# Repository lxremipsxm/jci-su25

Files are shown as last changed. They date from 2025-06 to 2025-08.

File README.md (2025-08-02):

# Card Badging Mechanical Automation

## Phases
+ **Design Phase** (5/26/25 to 5/30/25)
+ **Component Setup and Testing** (Estimated: 6/4/25 to 6/6/25; Actual: 6/2/25 to 6/20/25)
+ **Construction** (Estimated: 6/20/25 to 7/1/25)
+ **Automation** (Estimated: 7/7/25 to 7/20/25)
+ **Refinement + Adding Features**

## Goals
The primary goal of this project is to create an automation that badges card for a user in a certain order. This design must be scalable, quick, and easy to use. It should be flexible as well; my intention is to make this as easy for a team to use as possible.

---

## Design Phase 

### Protoype Design (5/26)

For my first prototype, I'm creating a solution that can badge 16 cards in quick succession. It consists of a drum rotated accurately by a stepper motor. The drum has 16 holes that fit card slots into them, which are lifted by a cam (operated by a micro servo) into the range of a stationary reader. 

In order to scale this design up, an additional cam must be placed under each new reader. Since micro servos are inexpensive, this design is simultaneously cost effective. Ideally, the larger the drum, the more readers can be incorporated.

##### Onshape

This is my first time using Onshape. I spent about a day learning Onshape and how to create models accurate to scale. I then set out to create the models by sketching designs on faces and extruding them as necessary. Throughout the process, the idea behind the design remained relatively unchanged, but I made one significant revision: making the range of motion of the cams a little larger and moving the readers further away from the cards in order to prevent interference/reading multiple cards accidentally. I've also tried to use mates in my model. `Revolute_1` and `Revolute_2` in the Onshape document are fully functional and can be animated, but Onshape does not have a way for me to test a complete workflow.

##### Print (6/2)

I've sent the `.stl` files to be printed by [Robu.in's 3D printing service](https://robu.in/product/3d-printing-service/), which I will receive within a week's time (~6/9/25). The print file is saved as `Assembly2_ver3.stl` in the `3D/` directory, and the final product will look like the contents of `Prototype_Assembly.stl`. Find the Onshape document [here](https://cad.onshape.com/documents/6fe5cb060711fa738a919116/w/fa28f828e5c3d9cb04d2cd20/e/b66991c36ce5bdb22e432e13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) (you will need to sign in to view it). 

**Updates**

6/4/25: The print has been delayed, but I will move on to testing components and creating libraries to make the final product easier to construct.

6/9/25: The print was cancelled and refunded because I provided parts that were too large for the printer. The latest print file is stored in `Assembly2_ver4.stl`, in which I've reduced the height of the card slots and increased the size of the cam lift range instead. The prints will hopefully come in by next week (6/16 to 6/20).

---

## Component Testing 

Component List (tentative): Arduino UNO(1), Tower Pro 9g Micro Servos(4), NEMA 17 Stepper motor(1), DRV8825 stepper motor driver(1), 2N7000 N-MOSFETs(4), LM2965S buck converter(1)

### Makefile (6/2)

Since I'm using a more baremetal approach with this project, I'm skipping the Arduino IDE and managing functionality by editing register contents in the ATmega328p IC on-board. Additionally, I'll be using the `avr-gcc` toolchain to compile and flash my code onto the ATmega. For this, I've written a makefile that is heavily inspired by the makefiles I've had to use in college for my embedded systems course. Find the references [here](https://github.com/ProfMcL/ECE231).

### Servos 

I couldn't find any C libraries for the micro servos, unfortunately. However, I managed to create my own simple servo library that functions exactly the same. I've used a general purpose timer on the ATmega, 16-bit Timer 2, to generate a constant Fast PWM signal with a period of 20ms, which is required by the servo according to documentation, and a duty cycle that varies between 5% and 10%. The duty cycle of this PWM wave determines the angle the servo turns to. My function is constructed in such a way that it takes an input from 0 to 180 degrees, maps it to milliseconds, and adjusts the duty cycle by changing the value the timer waits till before it sets the PWM to `LOW` again.

The next step is to create a way to control four servos with the same timer. This is possible, but it requires some tweaking of my library to include taking a servo number as input, as well as NMOSFETs in the circuit to redirect the PWM signal to these servos as required. I will also need to tweak *when* the signal is `HIGH` depending on the servo that is being addressed.

### Stepper Motor (6/9)

I'm currently waiting for the stepper motor driver to arrive (DRV8825). Until then, however, I will work on customizing a library for this driver. Find the library github repository [here](https://github.com/adrielluiz/drv8825_c/tree/main). According to the documentation, I need to provide implementations of setting pins to output and creating a `delay_us()` function. Fortunately, I can just use the `utils/delay.h` library to complete that part. 

I've included `drv8825.c` and its associated header in `lib/`, and I will modify it there. The original author has left in some misspellings of DRV8825 in method and type identifiers, which I have fixed.

The library readme recommends using a certain code structure, which I'll copy into `main.c`. 

Now, I'll modify `drv8825.c`, which contains the methods I need to customize to my chip architecture. Fortunately for me, I will need to connect 8 pins from DRV8825 into GPIO pins (the rest are for power/go into the motor directly), so I can use one full port on the ATmega, which is exactly 8 bits wide/8 pins wide. I'm going to use `PORTD`, as `PORTB` currently is being used for USART. This way, each pin on the DRV8825's right-hand side can be connected directly to PD0-PD7, making the definition of `stepper_pin_set()` incredibly easy to implement via simple bitwise operations. Since PD0-PD7 are organized perfectly in order on the board, the connections will also be satisfyingly clean.

Note that in `drv8825.h`, the `enum drv8825_drv_pins_e` typedef is ordered significantly differently than that of the original author in order to implement `stepper_pin_set()` as described.

Once the DRV8825 comes in, I can test the stepper and the driver simultaneously, and I can conclude this phase. 

Update(6/16/25): The driver component has come in. I completed testing on 6/18, primarily because I was trying to understand why my motor was not receiving any current from the drv8825 at all. Apparently I had misunderstood the pinout on the board. The pins 2A, 1A, 1B, and 2B are outputs to the stepper motor, in that order. The NEMA 17 stepper motor has four input wires, or two pairs of wires that connect to two electromagnetic coils in the inner workings of the motor. I was connecting each pair to the driver by number rather than letter; i.e. I connected one pair to 1A and 1B and another to 2A and 2B. This did not work, and I was about to return the driver, but after trying some permutations of the four wires, I realized that the combination that I needed to use was by letter, i.e. one pair to 1A and 2A, and another to 1B and 2B. 

### NMOSFETs (6/16)

For the NMOSFETs selecting the correct servo, I will need to create a breakout board, since they are so small. I'll use this both to test them and for the final construction. Additionally, I want to make it flexible, so that I can operate 1,2,3, or 4 servos depending on the workflow needed.

I'm thinking of using 4 pins on `PORTB`. Depending on the servos necessary, I can set `PORTB` with bitwise operations; however, I do need to consider moving multiple servos to different angles in the same 20ms period. In order to do this, I need to partition the 20ms period into 4 parts (one for each servo), and update the timer to increase or decrease the pulse width according to the angle. This means I will need to heavily modify my `servo_set_pos()` method. In addition to this, I will need to ensure that despite 'partitioning' the timer signal into four parts, each servo still receives a signal with period 20ms, or the servo will exhibit unexpected behavior.

For testing, I'll send a constant `HIGH` through the drain terminal, read the output on the source terminal, and constantly vary the gate voltage between 5V and 0V (1 and 0). The output should be exactly the same as the gate input(`HIGH` or `LOW`). I may also have to use resistors on the terminals depending on their rating. 

## Modification and Adjustments (6/24)

### NMOSFET Removal

I've further researched and tested the NMOSFETs; unfortunately, I won't be able to use them, as the process is too tenuous to perform consistently, especially when the stepper and other devices are factored in. This is a result of the servo's very restrictive functionality: it must constantly be supplied with a PWM signal of period 20ms. In order to implement the NMOSFET switching mechanism, each servo needs to be assigned 5ms of time for its dedicated duty cycle. However, my uart library and any delays that I incorporate into the design will create tiny delays in the lower level workings of the chip. With the context of 20ms, a small delay could be significant. Overall, the 20ms requirement will not always be satisfied because my ATmega will be busy handling other tasks while driving the servos, which means they will be jittery, leading to an unsatisfactory, slow solution.

Instead, I will use a second timer on ATMega328p. This will be significantly more straightforward, as each timer has two PWM outputs, and I can simply modify duty cycles depending on the servo that needs to rotate. Now, I'm faced with additional topics to address.

First, I only have one 16-bit timer on the ATmega328p, called Timer1. The other two timers, Timer0 and Timer2, are 8-bit timers. It is recommended not to use Timer0, as it is involved in core processes, such as delays. Therefore, I need to use one 16-bit timer and a 8-bit timer. Each timer has two outputs that can be controlled independently(OCxA and OCxB), so that's four servo motors. To make functionality consistent, I will emulate Timer2 (8bit) as closely to Timer1 as possible. If this does not work, I have a ATmega2560 that I can swap the ATmega328p with. Unlike the 328p, it has four 16-bit timers, and will be much simpler to work with.

Second, I have to consider moving some of the pins around. PD3 is OC2A, or output compare 2A. This is one of two outputs from Timer2. Since this pin is irreplacable, I will 'shift' some pins on the DRV8825 up one pin, and solder the EN pin to ground permanently. I'll use the SLP pin to reduce power usage by the stepper motor instead.

### Power Adjustments 

I would like the final design to be convenient to use. A single power supply would be extremely useful in that case, rather than supplying the ATmega with a separate USB 5V DC supply, I just power the entire thing with the 12V being used to power the stepper motor. For this, I'm ordering a buck converter, that efficiently and reliably 'steps down' the input voltage to a smaller output voltage. I'm going with a LM2596S buck converter and will connect it in parallel to the stepper motor input power coming in from the 12V DC supply. The output can then go to the Arduino UNO's Vin pin. 

I will also use this supply to power the four servos, as they each can spike at 700mA+ under load, potentially causing errors in logic if all of them are powered by the UNO. Additionally, I will include a 470-1000uF capacitor to smooth out current.

### Servo Library

I need to modify my `servo_set_pos()` method to take another parameter, and use a simple switch-case block to modify the correct output compare register (OCRxA/OCRxB) based on which servo needs to be modified. I'm reusing the mapping from degrees to milliseconds from the previous implementation of this method. 

I've decided this is how I will connect my servos:

Servo 1: OC1A - PB1 (Arduino D9)

Servo 2: OC1B - PB2 (Arduino D10)

Servo 3: OC2A - PB3 (Arduino D11)

Servo 4: OC2B - PD3 (Arduino D3)

Additionally, I need to set up Timer1 and Timer2 to behave similarly. I will put both in Fast PWM mode with TOP = ICRx, and set TOP to 255. In other words, this makes the timer count to 255 before resetting/triggering an interrupt. I'll set both to 255, since the 8-bit timer can only count to 255 (even though the 16-bit timer can count to 65535). I then need to prescale both of them identically, such that after 255 counts, approximately 20ms have elapsed. 

Math:

$\frac{255}{(20*10^{-3})} = 12750$ counts/second

Original clock speed = 16MHz

$\therefore \frac{16000000}{12750} = 1254$

The maximum prescaler value on the timers on the ATmega328p is 1024. If we use 1024 as the prescaler for the timer clock, it results in a period of 16.4ms. This will not work; instead, I'll use an Arduino Mega, with a ATmega2560, and use two of its four timers. 

### Adaptation for ATmega2560 (7/1)

Since I am moving everything to an ATmega2560 for the additional timers, I have several things to update: the makefile, the DRV8825 `stepper_pin_set()` function, and the custom servo library. I will make these changes in a directory labeled `Final_Build/`, where I will store all the code that is fully functional and ready to go.

I will use the following pins on the 2560:

Pin name  |  Purpose

PortF 0:7 | DRV8825 EN:DIR

OC1A(PB5) | Servo 1 PWM

OC1B(PB6) | Servo 2 PWM

OC1C(PB7) | Servo 3 PWM

OC3A(PH3) | Servo 4 PWM

OC1x means Timer1 and OC3x means Timer3; both timers are 16-bit, and can easily manage a 20ms period waveform. Since the DRV8825 `stepper_pin_set()` function is adapted for a single port, I don't need to make too many changes(I just have to change `PORTD` to `PORTF`)

While modifying the makefile for the 2560, I ran into a slight issue. The programmer that is typically used by the Arduino IDE to flash to the Arduino Mega 2560 is called 'wiring', only offered in newer versions of `avrdude`, the tool I use to flash and compile. My version of `avrdude` was last updated in 2010, so it didn't have 'wiring' as an option. It took me a while, but I found a workaround, where I call the avrdude version used by the IDE instead of the one I have installed (also in my PATH). In the makefile, this shows up as two file paths, one for `avrdude.exe` and the other for `avrdude.config`, which are configurations I need to use the latest version. None of this will affect the actual `.hex` flashed to the ATmega, but I decided it was important to mention this roadblock. 

---

## Construction (6/26)

While modifying the servo design, I am simultaneously working on constructing the mechanism for the final automaton. I've attached the stepper to the center of a base made of wood, and have fixed the drum to the top of the motor. I've marked the areas where the servos need to go, and have cleared out the area which they require to rotate. I've sanded down the card slots for smoother up-and-down motion in the drum (the original texture from the 3D printer was hindering movement significantly). If required, I will apply grease to the slots, but with the current loose fit of the slots into their holes, I believe that's not entirely necessary. While doing this, I realized I should have rounded the edges of the sticks connected to the card slots in the 3D model for easier movement when in contact with the pear cam, but I sanded down the edges to a satisfactory degree; combined with the restricted degrees of freedom offered by the drum, this will work just fine. 

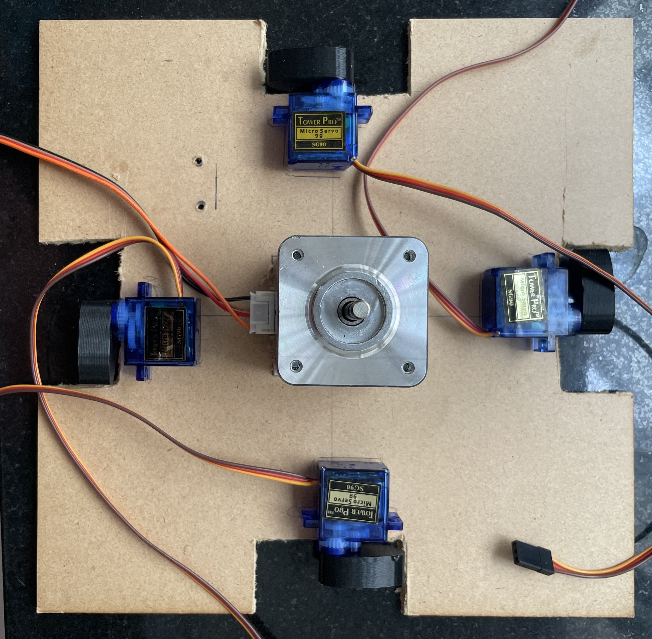
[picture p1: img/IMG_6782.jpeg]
Construction Process Update 1


Along with this, I've constructed a clean perfboard with all the functionality discussed so far: 

The DRV8825 connects directly into the board, and an array of 8 pins goes from the UNO PortD (Digital pins 0 to 7, excluding 3) into 8 female headers into the driver. **Note**: The design has been switched to an Arduino Mega. Therefore, these 8 pins will alternatively be connected into PORTF on the ATMega2560, digital pins 54 to 61. 

There are four sets of 3 male headers in the board for connections to the servo motors. These have their GND pins connected together in parallel. Similarly, the VCC pins are connected in parallel. I've included additional male headers for GND and V+ connections as power rails on the perfboard(5 GND, 3 V+).  

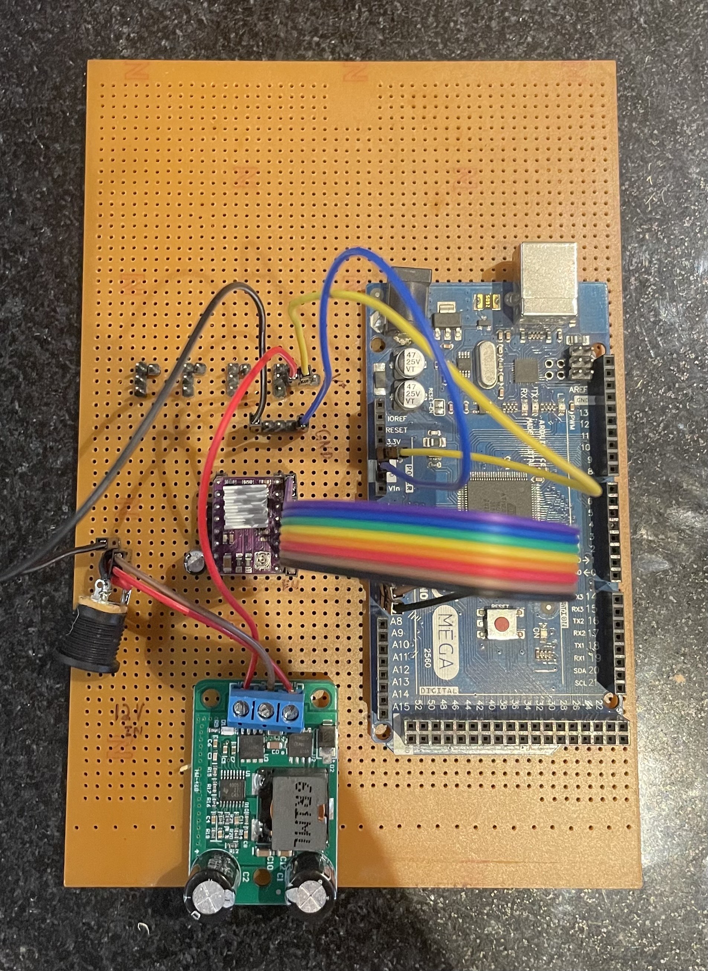
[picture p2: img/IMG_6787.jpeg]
Perfboard


Note that this design also includes the LM2596S buck converter (the green board connected to 12V in), which supplies the MEGA through its 5V pin.

(7/2): I've added guide rails to each card slot to ensure they don't spin when they are being raised.

---

## Automation, Features and Refinement (7/3)

The final step is to have the stepper and servos work simultaneously. 

There was a slight issue in calculating the pulse width being sent into the DRV8825's STEP pin, which made rotations and the entire `drv8825_move_steps()` function inaccurate. The inaccuracy was in the division: the original author included a divisor of the number of steps the user wanted to move. However, this variable is already being used to generate the pulse width in the `for` loop. Instead, in the calculation, I replaced the `steps` parameter with the `steps_per_revolution` variable defined in the driver settings `drv8825_scr_t scr`, and this did the trick.

After some testing, I've determined that the number of (full) steps between each card slot is approximately 15. I will need to account for slight inaccuracies due to the limitations of a NEMA17 stepper motor, so I will most likely use the maximum number of microsteps (32 for this driver).

I'll define a function to convert card 'numbers' into the number of steps needed by the stepper to rotate to a card from it's current position. I will also need to keep track of which slot 'number' the stepper is at, while ensuring that the stepper takes the fastest route possible (i.e. rotates in the direction that is most efficient movement-wise).

### Keypad Update (7/5)

I've included a keypad in order to have a simple user interface; it is connected directly through PortA on the ATmega2560, pins PA0 to PA7. Currently, I've included subroutines straight in the `Final_Build/main.c` file, but I will probably move it into library files later and store them in `Final_Build/lib/`. The numbers correspond to card slots and the letters A through D correspond to the reader number/servo number.

Edit(7/10): I've decided I don't really need to create a library form for the keypad functionality, and it makes it easier to refer to when I'm coding the interface to the stepper motor rotation.

Over this week, I've further modified the main method to take input from the keypad and signal the stepper to move the appropriate number of slots forward or backward. The direction that the MCU decides is the shortest path (for example, rather than go 15 slots forward to get from 1 to 16, move back one slot). 

I had a ton of issues debugging the keypad, especially with adding constraints that ensure users enter values in the correct format. The biggest challenge was when my `current_pos` variable, which tracks the current card position at reader A was not updating. Since the movement amount is fully dependent on this value, everything I entered through the keypad always gave me an incorrect result. I later realized that I had accidentally run an `sprintf()` on a buffer with an allocated memory that was too small for the string I wanted to copy to the buffer, leading to `stepper_move_to_pos()` (the function involving `current_pos`) crashing. Since I was relying on pointers to modify the value outside the subroutine, the crash was catastrophic to the operation of my system. Eventually, I removed the `sprintf()` from the function to place debug messages outside the subroutine and realized everything was working again, which is how I deduced that was broken.

### SSD1306 Update (7/13)

Since UART will not be visible to a user during the use of the system (it's not possible to connect the Arduino to a computer through USB while simultaneously powering it via the LM2596S buck converter), I'm including a SSD1306 that will display useful information to a user, such as error codes and input so far.

### Refinement (7/14)

I've completed just about everything that is necessary for full, uninterrupted operation of the system. However, I'm running into a lot of accuracy issues regarding the rotation amount of the stepper per slot. I modified the  `stepper_move_to_pos()` function to calculate the *exact* amount needed for an accurate rotation, but it seems the calculation is either incorrect or the drv8825 library is faulty. I've checked the library and even replaced the `_delay_us(pulse_width_us)` with a Timer4 delay, but this only made the drum rotate faster with arguably no improvement to accuracy whatsoever. 

I'm securing the drum more tightly on the shaft of the stepper, just in case the drum gets dislodged at every rotation, since I've noticed that the drum is unreasonably easy to rotate independently from the shaft even when the stepper is activated. For context, when the stepper is activated, it has a 'holding torque' that keeps it from moving out of its current step. If this is not the problem, it is probably a mechanical inaccuracy which I will need to use software to override, probably by adding additional steps to each rotation amount.

Update (7/16): I have made the stepper as accurate as possible considering its mechanical inaccuracies. However, for more reliable operation, I have the main method put the stepper to sleep when not moving both to conserve power and to enable a user to slightly shift the drum back into a good position before running a new test case, as putting the stepper to sleep turns off its holding torque until re-enabled.

---

## Final Build

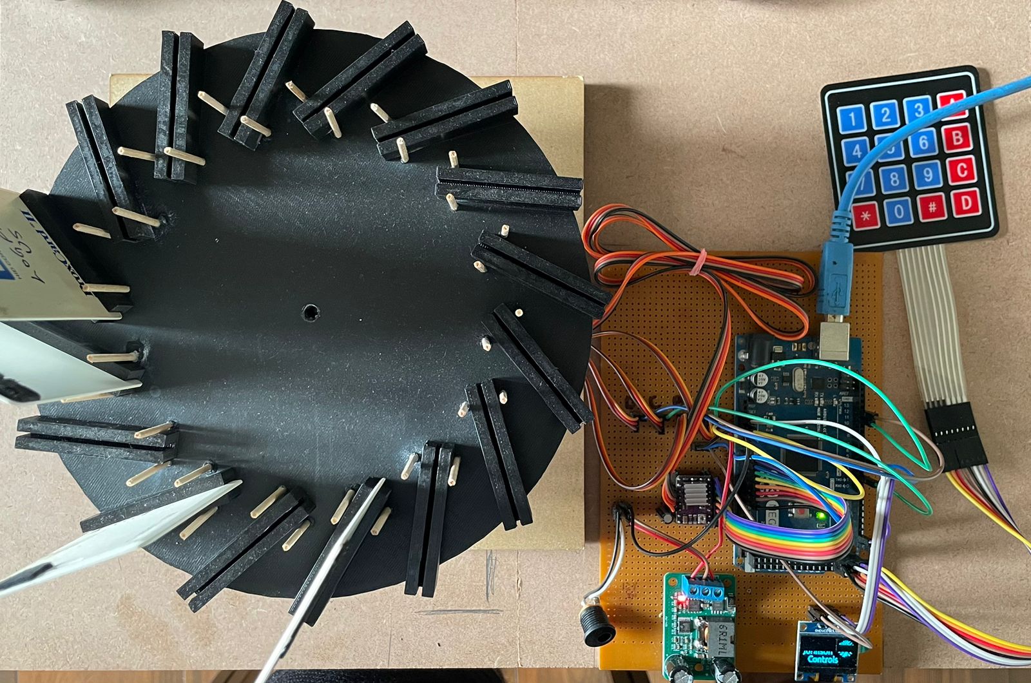
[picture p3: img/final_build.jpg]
Final Build Appearance


## Final Pin Arrangement Reference

### Arduino Mega (out)

Servo A Data: PB5 (Digital pin D11)

Servo B Data: PB6 (Digital pin D12)

Servo C Data: PE4 (Digital pin D2)

Servo D Data: PE3 (Digital pin D6)

DRV8825 DIR->EN: PORTK/PK0->PK7 (Analog pins A0 to A7)

Keypad: PORTA/PA1,3,5,7,6,4,2,0 (Digital pins D23, 25, 27, 29, 28, 26, 24, 22)

OLED Power: GND, 3.3V pin

OLED SCL: PD0 (Digital pin D21)

OLED SDA: PD1 (Digital pin D20)

### Arduino Mega (in)

LM2596S Buck Converter 5V OUT: 5V pin (via V+ rail)

GND from 12V female jack: GND pin (via GND rail)

### DRV8825 (out)

1A, 2A, 1B, 2B: NEMA 17 stepper motor

### DRV8825 (in)

VMOT: V+ from 12V female jack

GND: GND from 12V female jack

**Note**: a capacitor is soldered across the above connections to avoid voltage spikes when the system is powered on.

Logic GND: GND rail

### Servos (in)

VCC (red wire): V+ rail

GND (brown wire): GND rail

### LM2596S Buck Converter (in)

IN: 12V from 12V female jack

GND: GND from 12V female jack

---

## Instructions for Use

1. Input the card number to be read followed immediately by the reader name, then press "*" to confirm the selection. The format should be "nnX", where nn is a number between 1 and 16, and X is any letter on the keypad(A-D).

2. Input the reader name thrice (format XXX) to have all 16 cards read at the selected reader. "*" to confirm the selection. 

3. In the case a user enters something in the wrong format, the OLED will return a message indicating what was wrong with the input.

4. "#" is a backspace key.

---

## References

1. [Sparkfun 4x4 Membrane Keypad Reference Manual](https://cdn.sparkfun.com/assets/f/f/a/5/0/DS-16038.pdf)

2. [Tower Pro 9g Micro Servo Datasheet](https://www.friendlywire.com/projects/ne555-servo-safe/SG90-datasheet.pdf)

3. [Arduino Mega Rev3 Pinout](https://devboards.info/boards/arduino-mega2560-rev3)

4. [DRV8825 Tutorial](https://lastminuteengineers.com/drv8825-stepper-motor-driver-arduino-tutorial/)

5. Notes from UMass Amherst ECE231, taught in the spring semester of 2025

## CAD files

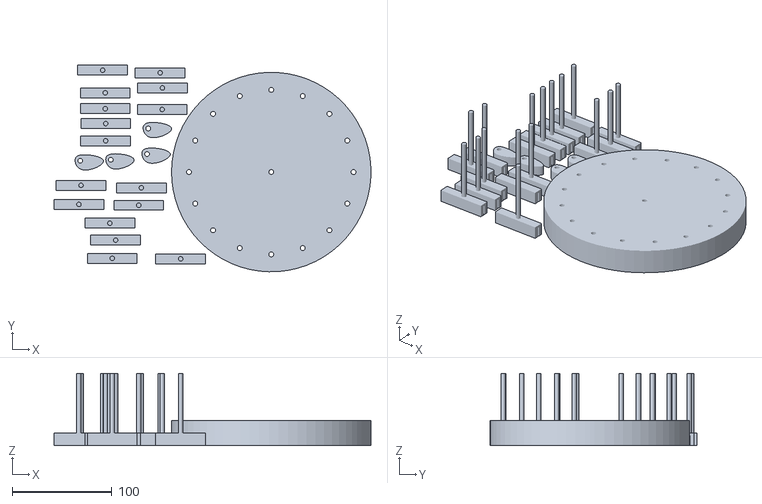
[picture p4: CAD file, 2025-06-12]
3D_Models/Assembly2_ver4.stl
317.8 x 207.1 x 72.5

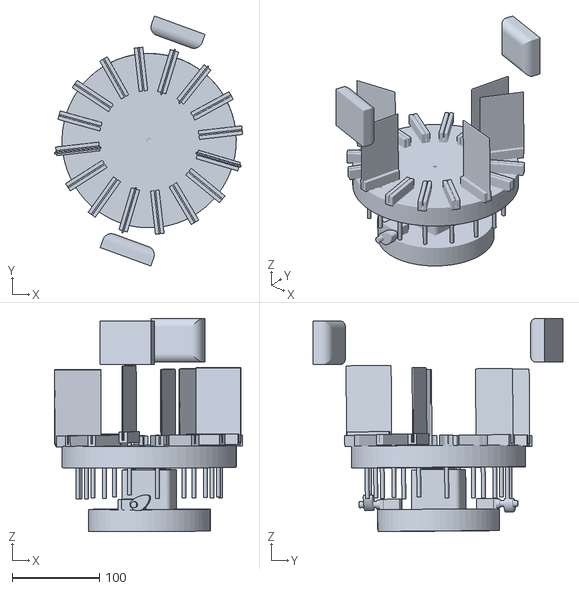
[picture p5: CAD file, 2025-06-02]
3D_Models/Prototype_Assembly.stl
216.2 x 286.9 x 244.6

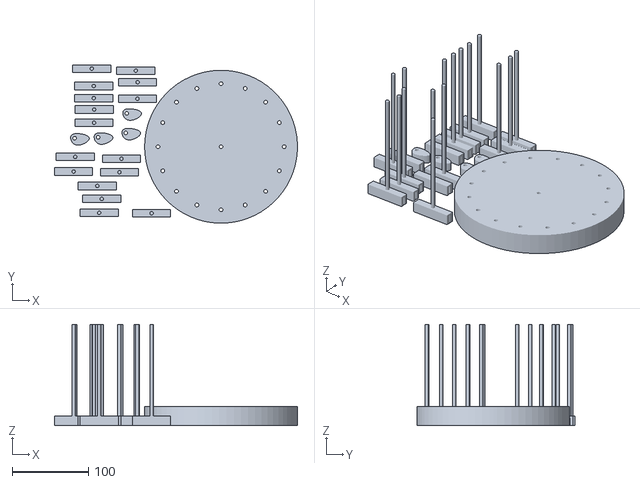
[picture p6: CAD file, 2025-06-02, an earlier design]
3D_Models/Assembly2_ver3.stl
317.8 x 207.1 x 132.5

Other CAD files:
3D_Models/Assembly2_ver2.stl
3D_Models/Assembly2.stl

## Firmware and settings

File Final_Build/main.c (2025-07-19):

/*Siddharth Vasudevan
Final_Build/main.c

Intended for complete build

Comments
--------
6/30/25: Created file
*/


//-----Includes-----//
#include <avr/io.h>
#include <stdio.h>
#include <util/delay.h>
#include <stdint.h>
#include <stdbool.h>
#include <stdlib.h>
#include <string.h>

//-----Libs-----//
#include "lib/uart.h"
#include "lib/servo.h"
#include "lib/drv8825_2560.h"
#include "lib/SSD1306.h"


//-----Servo Declarations-----//
void servo_raise(char servo){
    servo_set_pos(servo,50);
    _delay_ms(400);
    servo_set_pos(servo,0);
    _delay_ms(100);

}

//-----Stepper Declarations-----//
static void stepper_pin_set(drv8825_drv_pins_t pin, bool state)
{
    //drv8825_drv_pins_t is an enum of ints. 
    //I will be using PF0-PF7 to control the stepper motor, so 
    //I can just map the pins directly to their own number.

    if ((DDRF & (1<<pin)) == 0){
        DDRF |= (1<<pin);
    }

    if (state) {
        PORTF |= (1<<pin);
    }
    else {
        PORTF &= ~(1<<pin);
    }
    

}

static void stepper_delay_us(uint32_t t_us)
{
    _delay_us(t_us);
}


//Driver config
static drv8825_drv_t drv =
{
    .pin_set = stepper_pin_set,
    .delay_us = stepper_delay_us,
};

//Driver Settings
drv8825_scr_t scr =
{
    .steps_per_revolution = 200,
    .microsteps = 1,
    .rpm = 200,
};



void stepper_move_to_pos(int new_pos, int *current_pos)
{   
    drv8825_set_slp_pin(true);
    if (new_pos > 16) new_pos = 16;
    if (new_pos < 1)  new_pos = 1;

    int diff = new_pos - *current_pos;
    
    if (diff > 8)     
        diff -= 16;
    
    else if (diff < -8) 
        diff += 16;

    uint16_t steps_per_rev = drv8825_get_steps_per_revolution() * drv8825_get_microsteps();
    uint32_t ideal_steps_per_slot = (steps_per_rev * 100UL) / 16UL;  // x100 for fixed-point
    uint32_t movement_steps = (ideal_steps_per_slot * abs(diff)) / 100;

    if (diff > 0)
        drv8825_move_steps(movement_steps, DRV8825_DIR_FORWARD);
    else if (diff < 0)
        drv8825_move_steps(movement_steps, DRV8825_DIR_BACKWARD);

    *current_pos = new_pos;
}


void read_card(int card, char reader, int *current_pos){

    //All this does is use the position at reader A to determine the positions of the other three readers,
    //since they have a constant difference of 4 slots between each. I'll create a wrap-around functionality
    //to easily work with the 1-16 cap I have set in stepper_move_to_pos().
    int new_pos=1;
    char move_servo = 1;

    switch (reader){
        case 'A':
            new_pos = card;
            move_servo=1;
            break;

        case 'B':
            new_pos = card-4;
            move_servo=2;
            break;

        case 'C':
            new_pos = card-8;
            move_servo=3;
            break;

        case 'D':
            new_pos = card-12;
            move_servo=4;
            break;
    }


        if (new_pos <= 0){
            new_pos += 16;    
        }

        stepper_move_to_pos(new_pos, current_pos);
        _delay_ms(100);
        servo_raise(move_servo);
}





//-----Keypad declarations-----//
const char keymap[4][4] = {
    {'1', '2', '3', 'A'},
    {'4', '5', '6', 'B'},
    {'7', '8', '9', 'C'},
    {'*', '0', '#', 'D'}
};

void keypad_init(){
    //Using Port A for keypad
    DDRA = (1 << PA1) | (1 << PA3) | (1 << PA5) | (1 << PA7); //first nibble for rows(output), second for columns (input)
    PORTA = 0xFF; //Pulls inputs HIGH and outputs 5V at outputs
}

char keypad_char() {
    char key = 0;

    while (key == 0) { //wait until character entered
        for (uint8_t row = 0; row < 4; row++) {
            // Set all rows HIGH
            PORTA |= (1 << PA1) | (1 << PA3) | (1 << PA5) | (1 << PA7);

            // Drive current row LOW
            switch (row) {
                case 0: PORTA &= ~(1 << PA1); break;
                case 1: PORTA &= ~(1 << PA3); break;
                case 2: PORTA &= ~(1 << PA5); break;
                case 3: PORTA &= ~(1 << PA7); break;
            }

            _delay_us(5);

            // Read column inputs 
            uint8_t col_input = 0;
            col_input |= (PINA & (1 << PA6)) ? (1 << 0) : 0; //if pin A6 high, bitwise or col_input with 0x01
            col_input |= (PINA & (1 << PA4)) ? (1 << 1) : 0;
            col_input |= (PINA & (1 << PA0)) ? (1 << 2) : 0;
            col_input |= (PINA & (1 << PA2)) ? (1 << 3) : 0;

            for (uint8_t col = 0; col < 4; col++) {
                if (!(col_input & (1 << col))) {
                    key = keymap[row][col];
                    break;
                }
            }
            if (key) break; //wait until a key is pressed
        }
    }

    
    return key;
}


void keypad_string(char *stringAddress){
    OLED_GoToLine(3);
    OLED_DisplayString("Input: ");

    char response;
    uint8_t len = 0;

    while (1){
        response = keypad_char();
        

        if (response == '*') {
            OLED_Clear();
            break;
        }

        if (response == '#') {
            if (len > 0) {
                len--;
                stringAddress[len] = '\0'; // Remove last character
            }
        }

        else if (len < 5){
            stringAddress[len++] = response; //concatenate with previous numbers entered
            stringAddress[len] = '\0'; //add null terminator
            
        }

        OLED_DisplayString("     ");
        OLED_GoToLine(4);
        OLED_DisplayString(stringAddress);

        _delay_ms(350);
    }
}

//-----SSD1306-----//
const char logo[1024] = {
    0x00, 0x00, 0x00, 0x00, 0x00, 0x00, 0x00, 0x00, 0x00, 0x00, 0x00, 0x00, 0x00, 0x00, 0x00, 0x00,
    0x00, 0x00, 0x00, 0x00, 0x00, 0x00, 0x00, 0x00, 0x00, 0x00, 0x00, 0x00, 0x00, 0x00, 0x00, 0x00, 
    0x00, 0x00, 0x00, 0x00, 0x00, 0x00, 0x00, 0x00, 0x00, 0x00, 0x00, 0x00, 0x00, 0x00, 0x00, 0x00, 
    0x00, 0x00, 0x00, 0x00, 0x00, 0x00, 0x00, 0x00, 0x00, 0x00, 0x00, 0x00, 0x00, 0x00, 0x00, 0x00, 
    0x00, 0x00, 0x00, 0x00, 0x00, 0x00, 0x00, 0x00, 0x00, 0x00, 0x00, 0x00, 0x00, 0x00, 0x00, 0x00, 
    0x00, 0x00, 0x00, 0x00, 0x00, 0x00, 0x00, 0x00, 0x00, 0x00, 0x00, 0x00, 0x00, 0x00, 0x00, 0x00, 
    0x00, 0x00, 0x00, 0xE0, 0xF0, 0x00, 0x00, 0x00, 0xF8, 0x80, 0x00, 0x00, 0xF8, 0xE0, 0x00, 0xC0, 
    0xC0, 0x00, 0x20, 0x00, 0x00, 0x00, 0x00, 0x00, 0x00, 0x00, 0x00, 0x00, 0x00, 0x00, 0x00, 0x00, 
    0x00, 0x00, 0x00, 0x00, 0x00, 0x00, 0x00, 0x00, 0x00, 0x00, 0x00, 0x00, 0x00, 0x00, 0x00, 0x00, 
    0x00, 0x00, 0x00, 0x00, 0x00, 0x00, 0x00, 0x00, 0x00, 0x00, 0x00, 0x00, 0x00, 0x00, 0x00, 0x00, 
    0x00, 0x00, 0x00, 0x00, 0x00, 0x00, 0x00, 0x00, 0x00, 0x00, 0x00, 0x00, 0x00, 0x00, 0x00, 0x00, 
    0x00, 0x00, 0x00, 0x00, 0x00, 0x00, 0x00, 0x00, 0x00, 0x00, 0x00, 0x00, 0x00, 0x00, 0x00, 0x00, 
    0x00, 0x00, 0x00, 0x00, 0x00, 0x00, 0x00, 0x00, 0x00, 0x00, 0x00, 0x00, 0x00, 0x00, 0x00, 0x00, 
    0x00, 0x00, 0x00, 0x00, 0x00, 0x00, 0x00, 0x00, 0x00, 0x20, 0xD8, 0x1C, 0x00, 0x80, 0xA8, 0xA9, 
    0x02, 0x00, 0xE0, 0x7F, 0x73, 0x00, 0x00, 0xF4, 0xE5, 0xE7, 0x00, 0x00, 0x19, 0xEF, 0xF3, 0xE1, 
    0xE0, 0x00, 0xF0, 0x30, 0x0C, 0x0C, 0x03, 0x80, 0xC0, 0xA0, 0x60, 0x00, 0x00, 0x00, 0x00, 0x00, 
    0x00, 0x00, 0x00, 0x00, 0x00, 0x00, 0x00, 0x00, 0x00, 0x00, 0x00, 0x00, 0x00, 0x00, 0x00, 0x00, 
    0x00, 0x00, 0x00, 0x00, 0x00, 0x00, 0x00, 0x00, 0x00, 0x00, 0x00, 0x00, 0x00, 0x00, 0x00, 0x00, 
    0x00, 0x00, 0x00, 0x00, 0x00, 0x00, 0x00, 0x00, 0x00, 0x00, 0x00, 0x00, 0x00, 0x00, 0x00, 0x00, 
    0x00, 0x00, 0x00, 0x00, 0x00, 0x00, 0x00, 0x00, 0x00, 0x00, 0x00, 0x00, 0x00, 0x00, 0x00, 0x00, 
    0x00, 0x00, 0x00, 0x00, 0x00, 0x00, 0x00, 0x00, 0x00, 0x00, 0x00, 0x00, 0x00, 0x00, 0x00, 0x00, 
    0x00, 0x00, 0x00, 0x00, 0x00, 0x00, 0x00, 0x04, 0x04, 0x83, 0x40, 0x48, 0x36, 0x04, 0x09, 0x00, 
    0x60, 0x5A, 0xFD, 0x3D, 0x03, 0x80, 0x78, 0x7F, 0xF7, 0xF3, 0x00, 0x00, 0xFF, 0xFF, 0xA9, 0xFF, 
    0x20, 0x03, 0x00, 0x00, 0x58, 0x48, 0xB7, 0x00, 0x00, 0x00, 0x40, 0xA0, 0xA0, 0x00, 0x00, 0x00, 
    0x00, 0x00, 0x00, 0x00, 0x00, 0x00, 0xFE, 0xBE, 0x00, 0x00, 0x80, 0xC0, 0xA0, 0xE0, 0x60, 0x60, 
    0xE0, 0x60, 0xC0, 0x00, 0x00, 0x00, 0xF6, 0xFD, 0xE0, 0x60, 0x20, 0x20, 0x80, 0x60, 0xC0, 0x00, 
    0x00, 0xE0, 0xE0, 0xE0, 0x60, 0x60, 0x60, 0xE0, 0xE0, 0xC0, 0x00, 0x00, 0xC0, 0xA0, 0x60, 0x60, 
    0x60, 0x60, 0x20, 0x00, 0x00, 0x80, 0x40, 0xA0, 0x20, 0x40, 0x40, 0x60, 0x60, 0x80, 0x00, 0x00, 
    0xC0, 0x60, 0xE0, 0x60, 0x40, 0x60, 0xE0, 0x60, 0xC0, 0x00, 0x00, 0x00, 0x00, 0x00, 0x00, 0x00, 
    0x00, 0x00, 0x00, 0x00, 0x00, 0x00, 0x00, 0x14, 0x1C, 0x05, 0x02, 0xC3, 0xA0, 0xA8, 0x2A, 0x7E, 
    0x2C, 0x07, 0x03, 0xA0, 0xF8, 0x67, 0xFD, 0xFF, 0x19, 0x01, 0xE0, 0x7C, 0xDF, 0xFE, 0xFB, 0x1B, 
    0x40, 0x00, 0x3E, 0xFC, 0x89, 0xC9, 0x84, 0x00, 0x00, 0x24, 0x04, 0xAB, 0x26, 0x00, 0x00, 0x00, 
    0x00, 0x00, 0x00, 0x00, 0x00, 0xE0, 0xDF, 0xF3, 0x00, 0x00, 0x3F, 0x7F, 0xD9, 0xE0, 0xC0, 0x80, 
    0xA0, 0xBF, 0x7F, 0x1B, 0x00, 0x00, 0xBD, 0xCF, 0x00, 0x00, 0x00, 0x00, 0x00, 0x73, 0xBD, 0x00, 
    0x00, 0xFF, 0xCF, 0xFF, 0x00, 0x00, 0x00, 0x84, 0xFF, 0xD6, 0x00, 0x00, 0xC3, 0xC7, 0xC6, 0xC6, 
    0xBC, 0xDC, 0x78, 0x00, 0x04, 0x3F, 0x7B, 0xE0, 0xC0, 0xC0, 0xC0, 0xE0, 0x7F, 0x3F, 0x06, 0x00, 
    0x18, 0xEF, 0xBF, 0x00, 0x00, 0x00, 0x00, 0xFE, 0xFD, 0x00, 0x00, 0x00, 0x00, 0x00, 0x00, 0x00, 
    0x00, 0x00, 0x00, 0x00, 0x00, 0x00, 0x00, 0x00, 0x00, 0x07, 0x07, 0x05, 0x05, 0x81, 0xA0, 0xC0, 
    0xF8, 0xC6, 0x67, 0x1F, 0x17, 0x05, 0x80, 0xE0, 0x78, 0xAE, 0xEF, 0xFF, 0xED, 0x0F, 0x1F, 0x01, 
    0x81, 0x60, 0x80, 0x80, 0x07, 0x0D, 0x16, 0x00, 0x10, 0x00, 0x00, 0x00, 0x00, 0x00, 0x00, 0x00, 
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
};


//-----Main method-----//
int main(void)
{

    //Setup
    OLED_Init();
    OLED_GoToLine(4);
    OLED_DisplayLogo(logo);
    uart_init();
    drv8825_init(&drv, scr);
    servo_start_pwm();
    keypad_init();


    //Stepper Settings
    drv8825_set_rpm(50);
    drv8825_set_steps_per_revolution(200);
    drv8825_set_microsteps(4);
    drv8825_set_microsteps_pin(4);
    int current_pos = 1; // current card at reader A

    char code[4];

    _delay_ms(2000);
    

    while(1){

        OLED_Clear(); //Clear display

        drv8825_set_slp_pin(false);

        OLED_GoToLine(1);
        char current[32];
        sprintf(current, "Card at A:%d", current_pos);
        OLED_DisplayString(current);

        code[0] = '\0'; //clear string  
        
        keypad_string(code);
        int len = strlen(code);




        if ((strcmp(code, "AAA") == 0) || (strcmp(code, "BBB") == 0) || (strcmp(code, "CCC") == 0) || (strcmp(code, "DDD") == 0)){

            char r = 'X';

            if (strcmp(code, "AAA") == 0){
                r = 'A';

            }

            else if (strcmp(code, "BBB") == 0){
                r = 'B';
            }

            else if (strcmp(code, "CCC") == 0){
                r = 'C';
            }

            else if (strcmp(code, "DDD") == 0){
                r = 'D';
            }
            
            else {
                //Do nothing
            }

            OLED_GoToLine(3);
            OLED_DisplayString("All cards to ");

            char readermsg[20];
            sprintf(readermsg, "Reader %c", code[0]);
            OLED_GoToLine(5);
            OLED_DisplayString(readermsg);

            int i;
            for (i=1; i<=16; i++){

                read_card(i, r, &current_pos);

                if (i%3 == 0){
                    drv8825_move_steps(4, DRV8825_DIR_FORWARD);

                }
            }
            
            continue;

        }

        if (len == 2){
            char temp[4];
            temp[0] = '0';
            temp[1] = '\0'; 
            strcat(temp, code);
            strcpy(code, temp);
            len += 1;
        }


        if (len > 3){
            uart_send_string("Invalid input. Input longer than three characters. \r\n");
            OLED_GoToLine(3);
            OLED_DisplayString("Max input 3 chars.");
           
        }

        else if ((code[len-1] != 'A') && (code[len-1] != 'B') && (code[len-1] != 'C') && (code[len-1] != 'D')){
            uart_send_string("Invalid input.  Enter a card number followed by the reader you would like it to be read by. E.g. 1A or 01A.\r\n");
            OLED_GoToLine(3);
            OLED_DisplayString("Incorrect Format.");
            OLED_GoToLine(5);
            OLED_DisplayString("e.g. 01A or 1A");
            

        }

        else {

            uart_send_string(code);
            uart_send_string("\r\n");

            char card_str[3];
            card_str[0] = code[0];
            card_str[1] = code[1];
            card_str[2] = '\0';

            int card_int = atoi(card_str);

            if ((card_int < 1) || (card_int > 16)){
                uart_send_string("Invalid input. Either your input card number is out of bounds, or you've entered a value with the wrong format. ");
                uart_send_string("Enter a card number followed by the reader you would like it to be read by. E.g. 1A or 01A. \r\n");
                OLED_GoToLine(3);
                OLED_DisplayString("Card value out of");
                OLED_GoToLine(5);
                OLED_DisplayString("bounds 1-16.");
                _delay_ms(700);
                continue; 
            }


            /*debug message
            char debug_msg[30];
            sprintf(debug_msg, "current pos before = %d\r\n", current_pos);
            uart_send_string(debug_msg);
            */

            char reader = code[2];

            char msg[32];
            sprintf(msg, "Card %d to reader %c", card_int, reader);

            OLED_GoToLine(4);
            OLED_DisplayString(msg); 
            read_card(card_int, reader, &current_pos);

            
            

            /*debug message 2
            char debug_msg2[32];
            sprintf(debug_msg2, "current pos after = %d\r\n", current_pos);
            uart_send_string(debug_msg2);*/
        

        }

        _delay_ms(500);
       

    }

    return 0;

}

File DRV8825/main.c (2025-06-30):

/*Siddharth Vasudevan
DRV8825/main.c

Testing DRV8825

Comments
--------
6/12/25: Created file, copying in recommended structure from https://github.com/adrielluiz
*/


//-----Includes-----//
#include <avr/io.h>
#include <stdio.h>
#include <util/delay.h>
#include <stdint.h>
#include <stdbool.h>

#include "lib/uart.h"
#include "lib/servo.h"
#include "lib/drv8825.h"



/*/-----Pin Mapping-----//
static uint32_t stepper_pin_mapping[8] =
{
    HW_MOTOR_STEP,
    HW_MOTOR_DIR,
    HW_MOTOR_RST,
    HW_MOTOR_SLP,
    HW_MOTOR_EN,
    HW_MOTOR_M0,
    HW_MOTOR_M1,
    HW_MOTOR_M2
};*/


static void stepper_pin_set(drv8825_drv_pins_t pin, bool state)
{
    //drv8825_drv_pins_t is an enum of ints. 
    //I will be using PD0-PD7 to control the stepper motor, so 
    //I can just map the pins directly to their own number.

    if ((DDRD & (1<<pin)) == 0){
        DDRD |= (1<<pin);
    }

    if (state) {
        PORTD |= (1<<pin);
    }
    else {
        PORTD &= ~(1<<pin);
    }
    

}

static void stepper_delay_us(uint32_t t_us)
{
    _delay_us(t_us);
}


//-----Driver config-----//
static drv8825_drv_t drv =
{
    .pin_set = stepper_pin_set,
    .delay_us = stepper_delay_us,
};

//-----Driver Settings-----//
drv8825_scr_t scr =
{
    .steps_per_revolution = 200,
    .microsteps = 1,
    .rpm = 200,
};

//-----Main method-----//
int main(void)
{
    drv8825_init(&drv, scr);
    uart_send_string("Stepper driver initialized.");
    uart_init();

    while(1){
        drv8825_move_steps(200, DRV8825_DIR_FORWARD);
        uart_send_string("Forward");

        stepper_delay_us(1000000);
        
        
    }

    return 0;
}

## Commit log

2025-06-02 .stl files (intended for 3D printer)
    [Assembly 2.stl, Assembly2_ver2.stl, Assembly2_ver3.stl]
2025-06-02 Rearranged project directory
    [Assembly 2.stl, Assembly2_ver2.stl, Assembly2_ver3.stl]
2025-06-02 Non-print assembly .stl file
    [Prototype_Assembly.stl]
2025-06-02 Managing git error with deletions
    [Assembly 2.stl, Assembly2_ver2.stl, Assembly2_ver3.stl]
2025-06-02 Tested basic arduino UNO functionality successfully, have makefile skeleton ready
2025-06-03 servo tests complete
2025-06-03 Converted servo methods to library
2025-06-12 Included drv8825 driver code + ATmega implementations
    [Assembly2_ver4.stl]
2025-07-02 Modified servo_start_pwm() method to include all four servos
2025-07-02 Renamed 3D/ to 3D_Models/
    [Assembly2.stl, Assembly2_ver2.stl, Assembly2_ver3.stl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]
2025-07-10 removing 3D/ directory (renamed to 3D_Models)
    [Assembly2.stl, Assembly2_ver2.stl, Assembly2_ver3.stl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]
